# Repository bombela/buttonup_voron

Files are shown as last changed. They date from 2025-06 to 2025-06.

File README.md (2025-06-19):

# Button up your Voron front doors

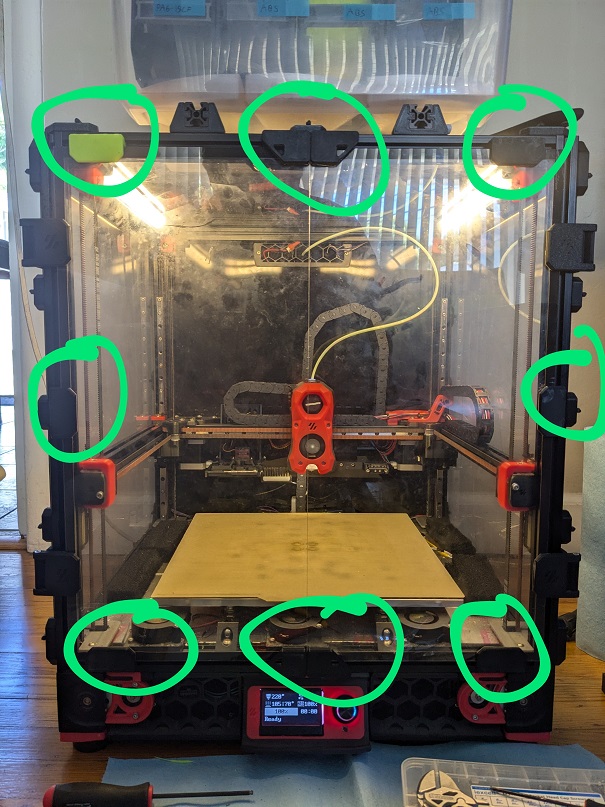
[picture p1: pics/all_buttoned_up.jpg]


The stock Voron doors do not always seal fully all around.
Especially at higher chamber temperature.
The doors have a tendecy to flex away from the frame ever so slightly.
Allowing relatively cold ambiant air to flow in, warping big prints.

This mod adds (a lot of) magnets for keeping the door sealed at all time at any temperature.
One part mounts on the frame, the mating part goes on the door.
Joined by four pairs of magnets.

This is enough magnets to seal well with those ubiquitous low quality magnets.
Though keep in mind that the worst ones will lose almost all strength beyond 70°C.

Be aware that with N52 grade magnets; rated for 80°C; the doors might become difficult to open at ambient temperature.
You can always start with half the magnets.

This mod also comes with handles for a consistantly tight seal at high chamber temperature all around.

## Printed parts and hardware (BOM)

All parts to prints are in the folders [STLs/](STLs/) and [STEPs/](STEPs/) (your choice).
You will find variation for 5.8x2.8mm and 6.0x3.0mm magnets for the four parts.
As well as various door thicknesses (door + seal) for the part that mounts on the frame.

For the stock Voron2.4 you want the "6.0x3.0magnet_3.5mm_door" variant.

### Recommended full set

3 buttonup per doors in addition to the handles. See photo atop.

#### Printed parts
 - buttonup_frame ×8.
 - buttonup_door ×6.
 - buttonup_handle_a ×2.
 - buttonup_handle_b ×2.

#### Hardware
 - ~6x3mm magnets ×64.
 - M3x8mm (for 3.5mm doors. Longer for thicker door) ×8.
 - M3 hammer nut ×8.
 - VHB tape ~44x13mm ×6.
 - VHB tape ~27x13mm ×4.

### Per buttonup

You probably want 6 of them.

#### Printed parts
 - buttonup_frame ×1.
 - buttonup_door ×1.

#### Hardware
 - ~6x3mm magnets ×8.
 - M3x8mm (for 3.5mm doors. Longer for thicker door) ×1.
 - M3 hammer nut ×1.
 - VHB tape ~44x13mm ×1.

### For a set of four handles

#### Printed parts
 - buttonup_frame ×2.
 - buttonup_handle_a ×2.
 - buttonup_handle_b ×2.

#### Hardware
 - ~6x3mm magnets ×16.
 - M3x8mm (for 3.5mm doors. Longer for thicker door) ×2.
 - M3 hammer nut ×2.
 - VHB tape ~27x13mm ×4.

## Demo

https://github.com/user-attachments/assets/6517687b-0205-439a-93e8-213152b58843

## Details

The buttonup_frame adds clearance around the doors compared to the stock part. With the exception of the screw, which cannot possibly be moved. This reduces friction.

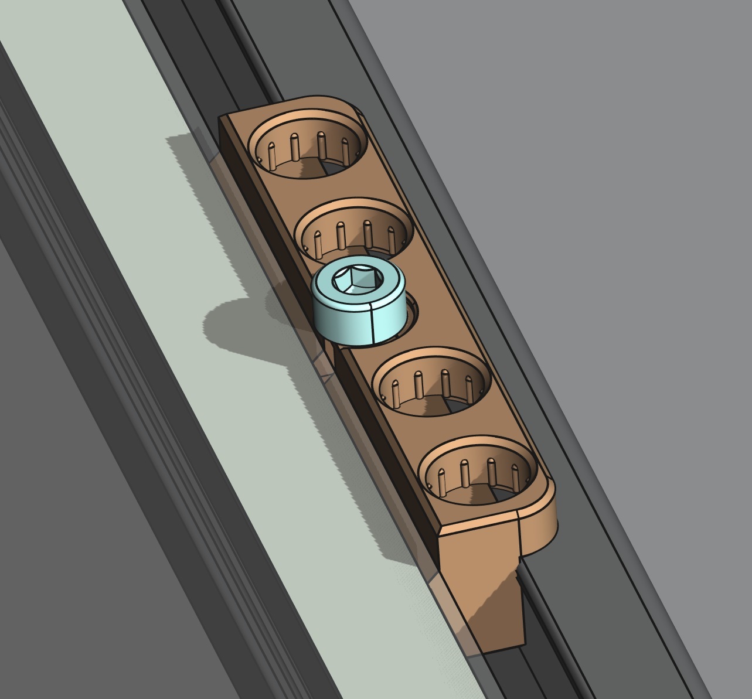
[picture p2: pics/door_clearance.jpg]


After ABS shrinkage, the top of the pocket should be about the same diameter as the magnet for a friction fit. Half-way down the pocket, 0.2mm ridges add extra interference for a tight fit.

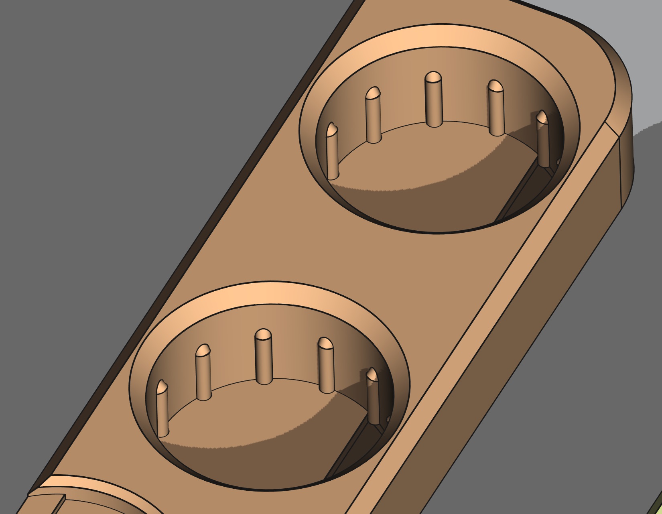
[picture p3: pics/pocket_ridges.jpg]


To make magnet removal easier, the frame part has holes to push them out from the back. The door parts have accomodation for a small flat head screw driver.

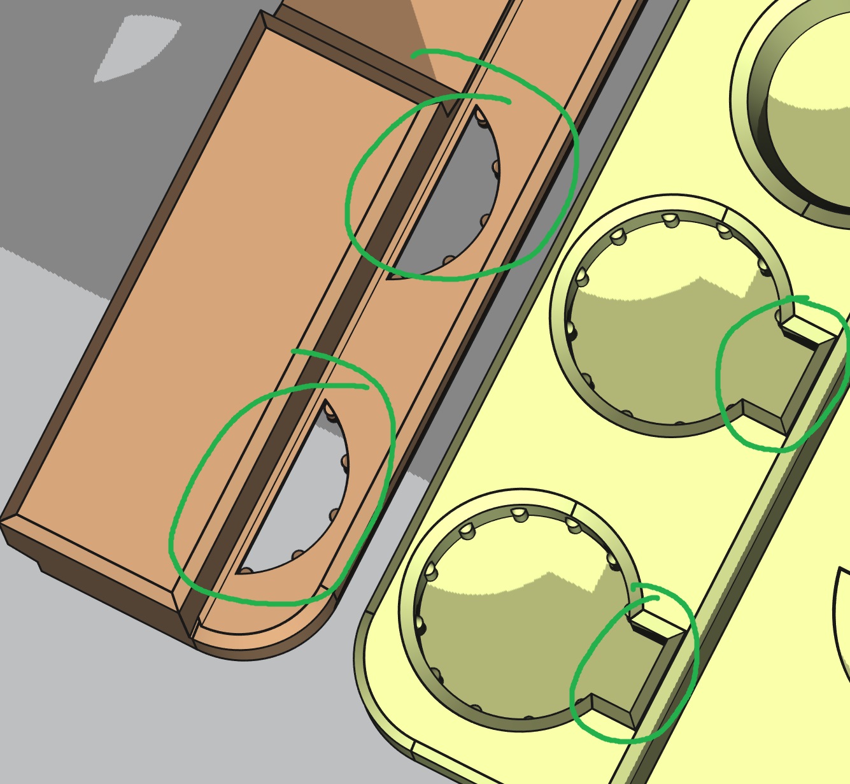
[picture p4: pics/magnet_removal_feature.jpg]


For easy identification; before and after printing; the magnet dimensions are written on every parts. With the addition of the door size on the frame part.

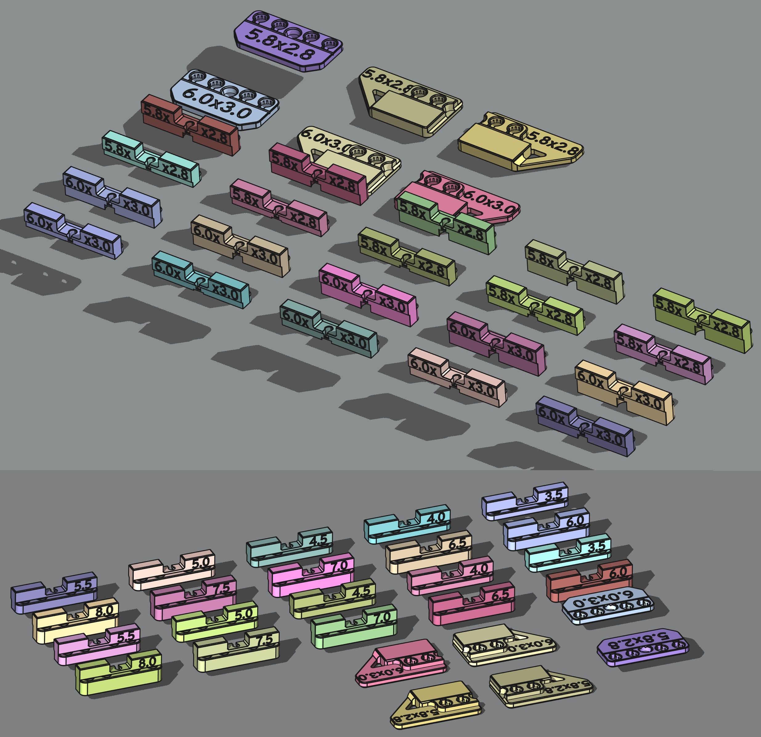
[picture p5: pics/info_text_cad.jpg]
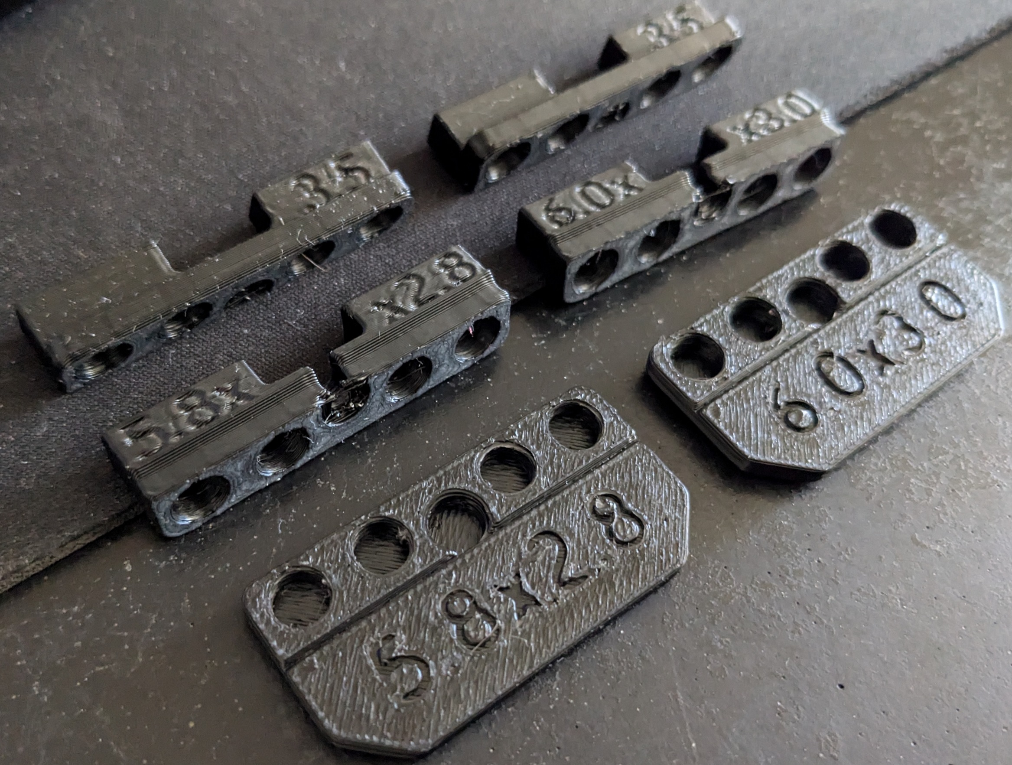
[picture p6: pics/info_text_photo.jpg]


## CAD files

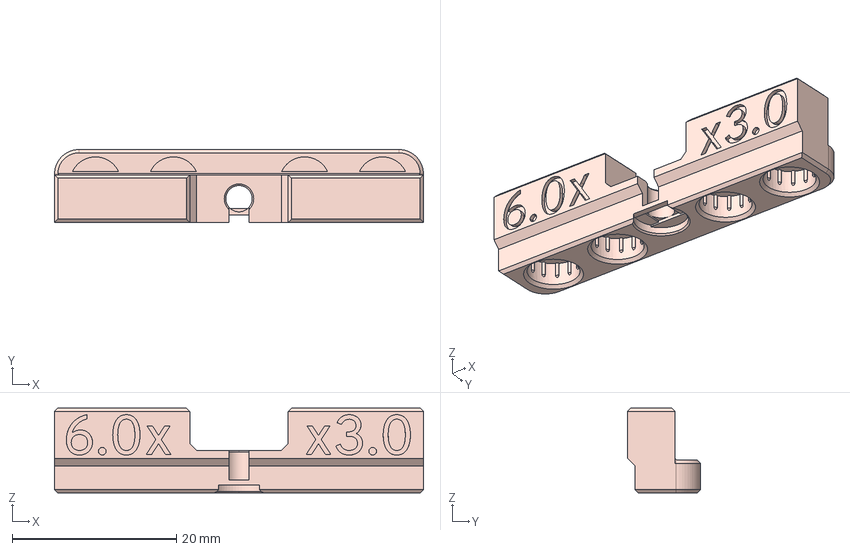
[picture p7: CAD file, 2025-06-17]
STEPs/buttonup_frame_6.0x3.0magnet_4.0mm_door.step
45.0 x 8.90 x 10.3 mm

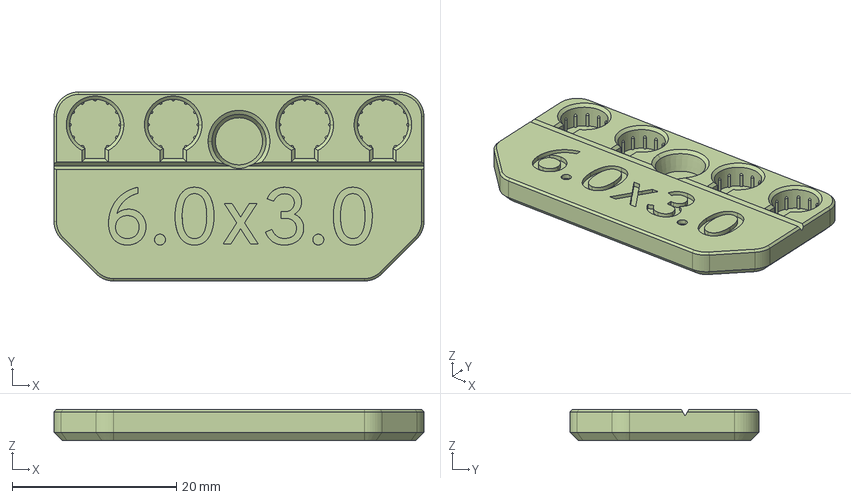
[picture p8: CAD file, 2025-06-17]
STEPs/buttonup_door_6.0x3.0magnet.step
45.0 x 23.0 x 3.80 mm

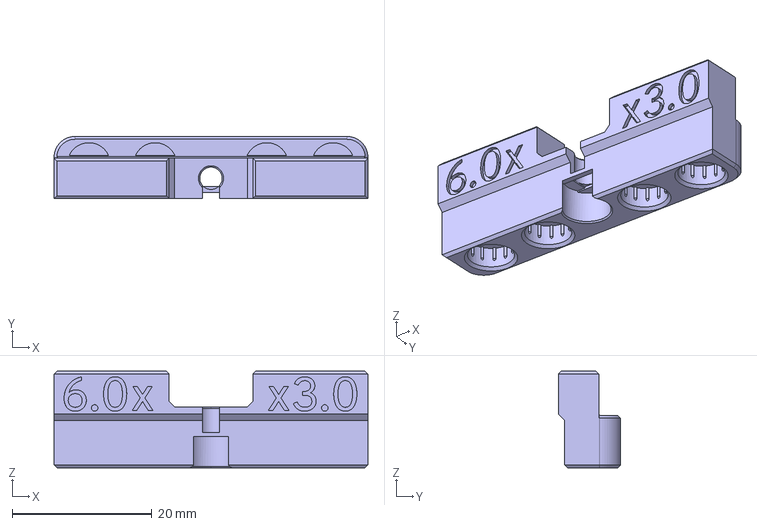
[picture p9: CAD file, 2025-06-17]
STEPs/buttonup_frame_6.0x3.0magnet_7.5mm_door.step
45.0 x 8.90 x 13.8 mm

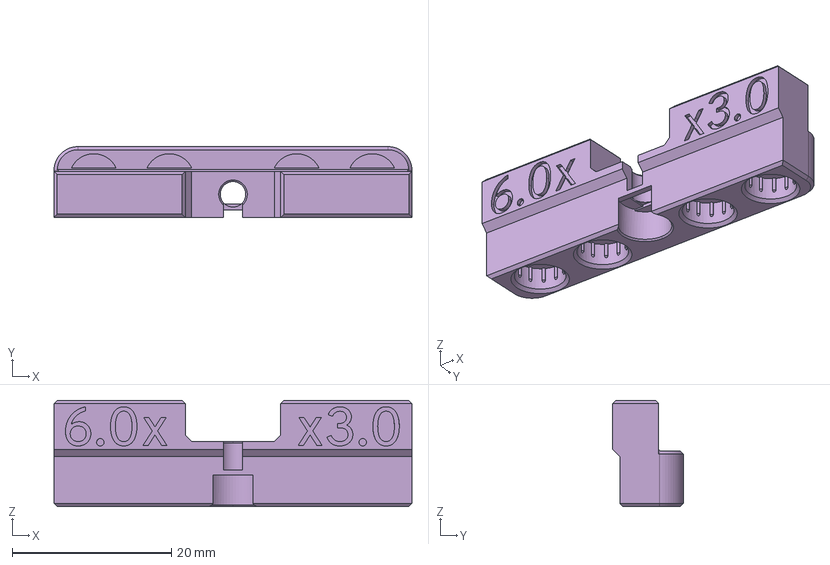
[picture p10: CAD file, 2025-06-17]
STEPs/buttonup_frame_6.0x3.0magnet_7.0mm_door.step
45.0 x 8.90 x 13.3 mm

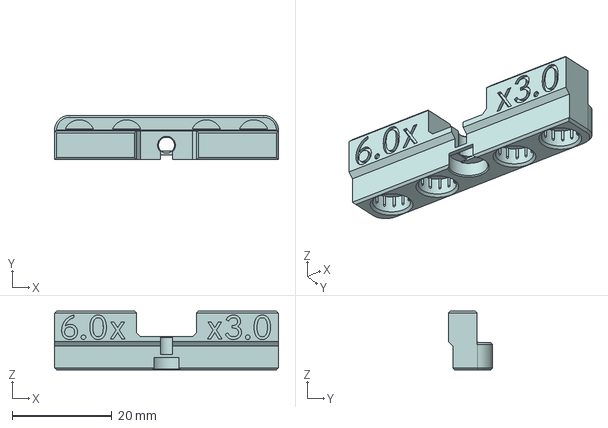
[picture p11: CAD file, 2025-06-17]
STEPs/buttonup_frame_6.0x3.0magnet_5.5mm_door.step
45.0 x 8.90 x 11.8 mm

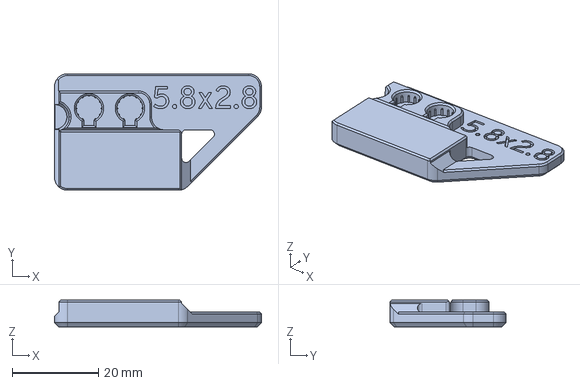
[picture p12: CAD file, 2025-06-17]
STEPs/buttonup_handle_b_5.8x2.8magnet.step
48.0 x 27.0 x 6.20 mm

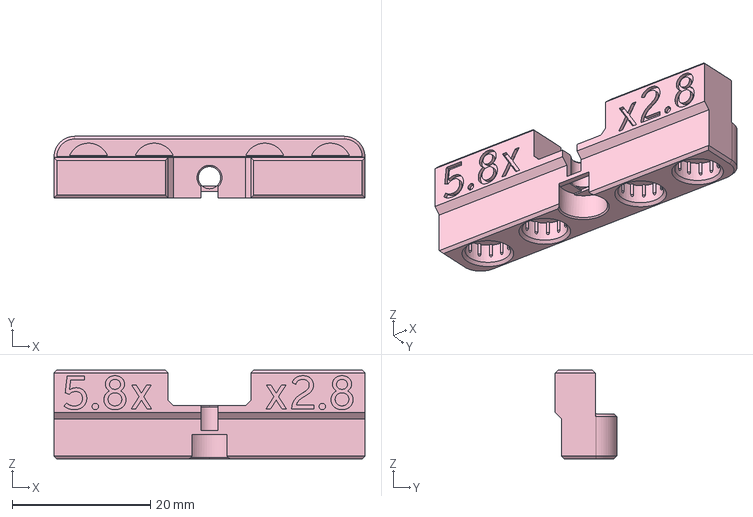
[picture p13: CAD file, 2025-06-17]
STEPs/buttonup_frame_5.8x2.8magnet_6.5mm_door.step
45.0 x 8.90 x 12.8 mm

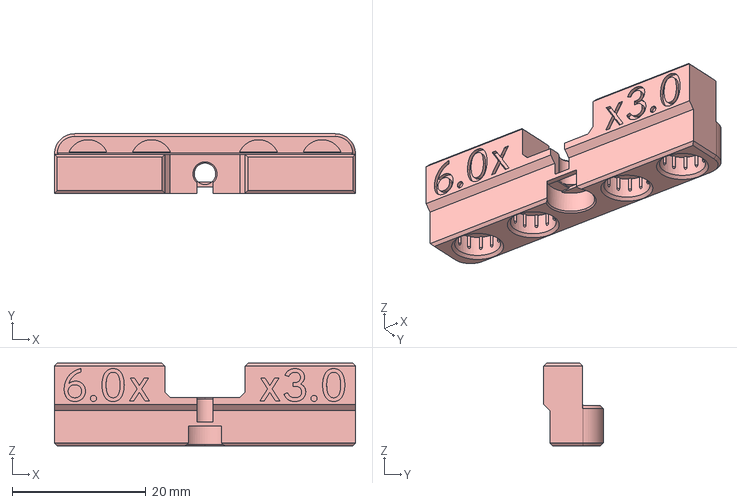
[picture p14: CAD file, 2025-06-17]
STEPs/buttonup_frame_6.0x3.0magnet_6.0mm_door.step
45.0 x 8.90 x 12.3 mm

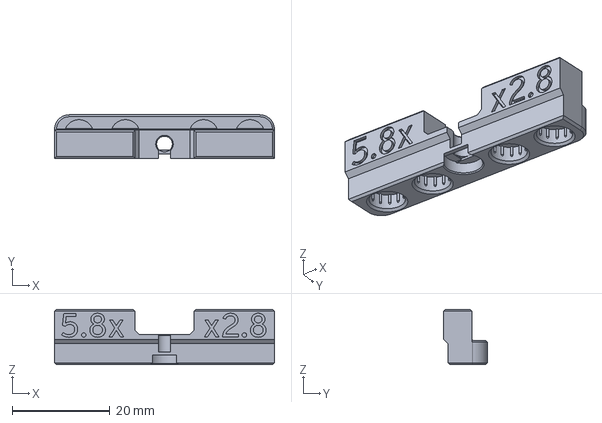
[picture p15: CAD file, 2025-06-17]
STEPs/buttonup_frame_5.8x2.8magnet_5.0mm_door.step
45.0 x 8.90 x 11.3 mm

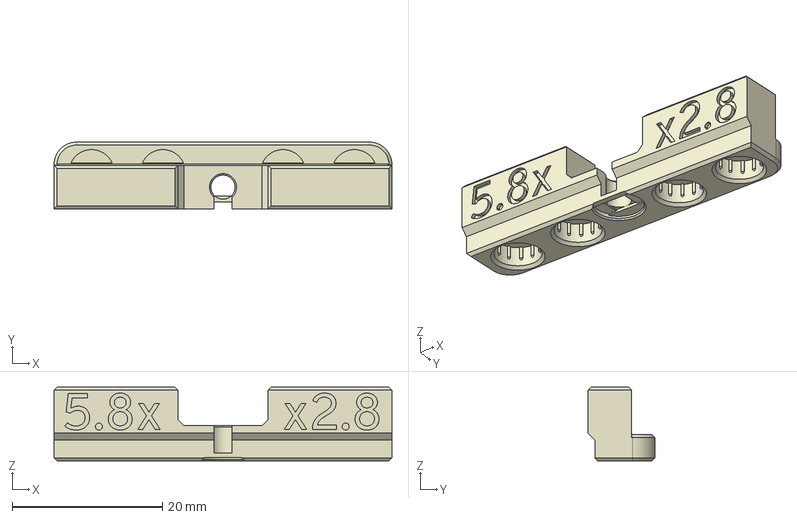
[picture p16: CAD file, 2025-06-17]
STEPs/buttonup_frame_5.8x2.8magnet_3.5mm_door.step
45.0 x 8.90 x 9.84 mm

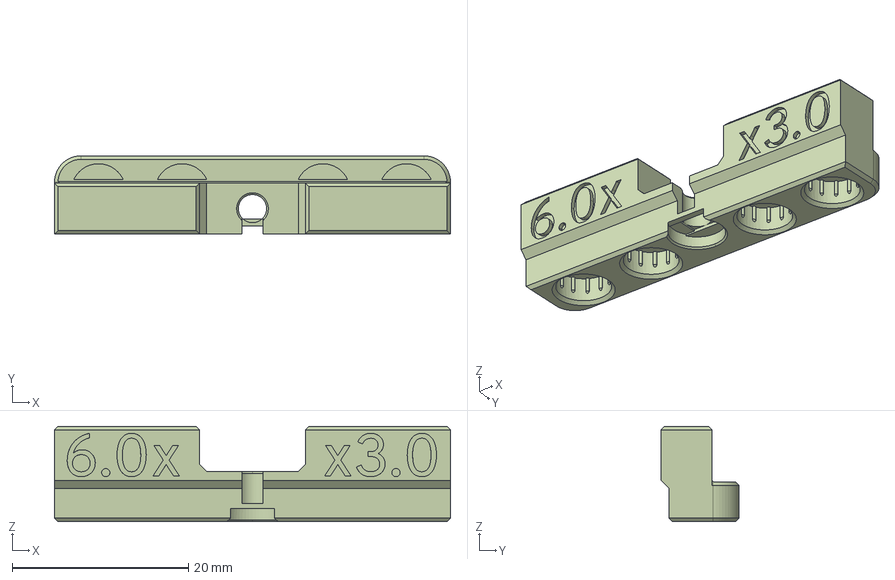
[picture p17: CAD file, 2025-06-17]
STEPs/buttonup_frame_6.0x3.0magnet_4.5mm_door.step
45.0 x 8.90 x 10.8 mm

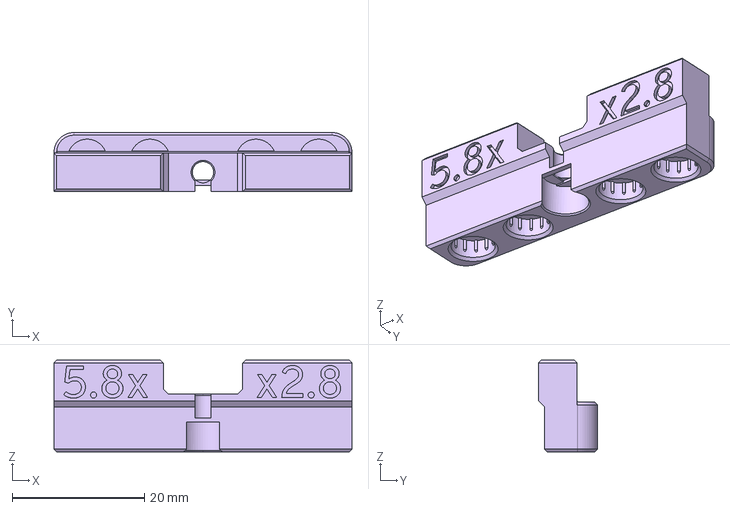
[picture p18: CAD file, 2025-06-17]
STEPs/buttonup_frame_5.8x2.8magnet_7.5mm_door.step
45.0 x 8.90 x 13.8 mm

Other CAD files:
STEPs/buttonup_frame_5.8x2.8magnet_5.5mm_door.step
STEPs/buttonup_frame_6.0x3.0magnet_6.5mm_door.step
STEPs/buttonup_frame_5.8x2.8magnet_8.0mm_door.step
STEPs/buttonup_frame_5.8x2.8magnet_6.0mm_door.step
STEPs/buttonup_frame_6.0x3.0magnet_5.0mm_door.step
STEPs/buttonup_door_5.8x2.8magnet.step
STEPs/buttonup_frame_5.8x2.8magnet_4.0mm_door.step
STEPs/buttonup_frame_5.8x2.8magnet_4.5mm_door.step
STEPs/buttonup_frame_5.8x2.8magnet_7.0mm_door.step
STEPs/buttonup_frame_6.0x3.0magnet_3.5mm_door.step
STEPs/buttonup_frame_6.0x3.0magnet_8.0mm_door.step
STEPs/buttonup_handle_a_5.8x2.8magnet.step
STEPs/buttonup_handle_a_6.0x3.0magnet.step
STEPs/buttonup_handle_b_6.0x3.0magnet.step
STLs/buttonup_door_5.8x2.8magnet.stl
STLs/buttonup_door_6.0x3.0magnet.stl
STLs/buttonup_frame_5.8x2.8magnet_3.5mm_door.stl
STLs/buttonup_frame_5.8x2.8magnet_4.0mm_door.stl
STLs/buttonup_frame_5.8x2.8magnet_4.5mm_door.stl
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
